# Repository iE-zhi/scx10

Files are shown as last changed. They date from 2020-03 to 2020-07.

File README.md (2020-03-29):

# scx10
 scx10 uart controller实现用串口控制SCX10攀爬车的基础动作，包括前进后退、左右转向和车灯控制。
 控制板接口：
 - 一路有刷电机
 - 两路舵机接口
 - 一个串口控制端
 - 一组前后灯和一组左右转向灯
 - 支持2S锂电池

控制板同样适用于符合以上条件的其他车辆及场景。

# 目录
- PCB: 电路板文件(AD18工程)
- program: 程序(keil5工程)
- 资料: 芯片资料

# PCB板尺寸
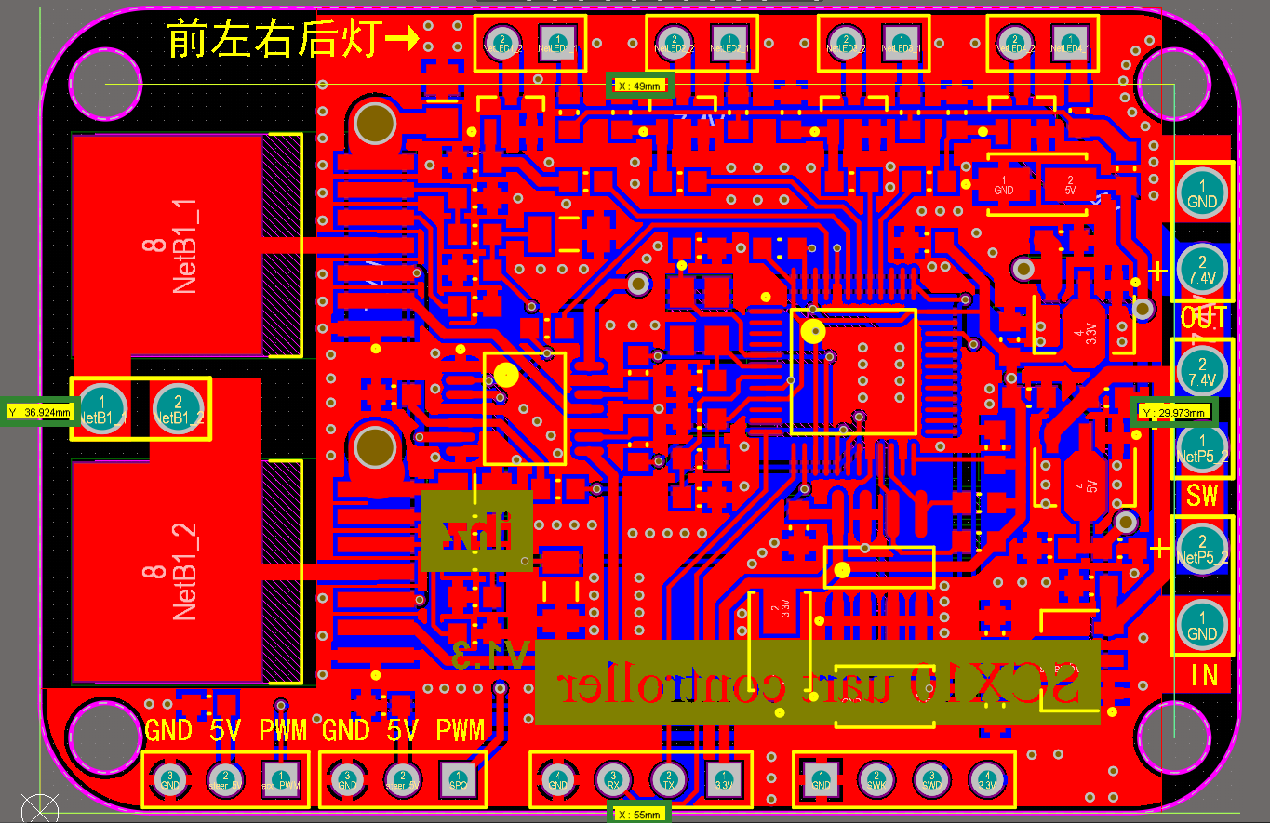
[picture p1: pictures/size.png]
pcb


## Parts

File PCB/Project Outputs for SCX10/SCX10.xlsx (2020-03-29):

Comment | Description | Designator | Footprint | LibRef | Quantity
Motor | Motor, General Kind | B1 | 7.4V | Motor | 1
0.1uF | Capacitor | C1, C2, C7, C9, C16, C19, C21, C22, C23, C24, C27 | C0603 | Cap | 11
4.7uF/16V | Capacitor | C3, C4 | 6-0805_M | Cap | 2
10uF | Capacitor | C5, C6, C8, C15, C18 | C0603 | Cap | 5
22uF | Capacitor | C10, C17, C20 | C0603 | Cap | 3
30pF | Capacitor | C25, C26 | C0603 | Cap | 2
3.6V | Schottky Diode | D1, D2 | C1206 | D Schottky | 2
SMAJ5.0CA |  | D3, D4, D5 | DO-214AC | SMAJ5.0CA | 3
F_LED | Header, 2-Pin | LED1 | HDR1X2 | Header 2 | 1
L_LED | Header, 2-Pin | LED2 | HDR1X2 | Header 2 | 1
R_LED | Header, 2-Pin | LED3 | HDR1X2 | Header 2 | 1
B_LED | Header, 2-Pin | LED4 | HDR1X2 | Header 2 | 1
Header 3 | Header, 3-Pin | P1, P2 | HDR1X3 | Header 3 | 2
Header 4 | Header, 4-Pin | P3 | HDR1X4 | Header 4 | 1
7.4V | Header, 2-Pin | P5, P6 | 7.4V | Header 2 | 2
SW | Header, 4-Pin | P7 | HDR1X4 | Header 4 | 1
NPN |  | Q3, Q4, Q5, Q6 | SOT23-3 | NPN | 4
0R/NC | Resistor | R2 | R0603 | Res2 | 1
240R | Resistor | R3, R4, R5, R6 | R0603 | Res2 | 4
10K | Resistor | R7, R8, R9, R10, R11, R12, R35 | R0603 | Res2 | 7
4.7K | Resistor | R13, R14, R15, R26, R27 | R0603 | Res2 | 5
1K | Resistor | R16, R17, R18, R19, R20, R21 | R0603 | Res2 | 6
510R | Resistor | R22, R23, R24, R25 | R0603 | Res2 | 4
SW-PB | Switch | S1 | 7.4V | SW-PB | 1
SN74LV125A-PW |  | U1 | TSSOP-14 | SN74LV125A-PW | 1
24C02 |  | U2 | SOP-8 | 24C02 | 1
BTN7971B |  | U3, U8 | INF-PG-TO263-7-1_L - Cloned | INF-BTN79XXX-PG-TO263-7-1-8 | 2
AMS1117-5V |  | U4, U6 | SOT-89 | AMS1117 | 2
AMS1117-3.3V |  | U5 | SOT-89 | AMS1117 | 1
STM32F103C8T6 |  | U7 | STM-LQFP48-L | STM32F103C8T6 | 1
8M |  | X1 | XTAL-8M | XTAL-8M | 1

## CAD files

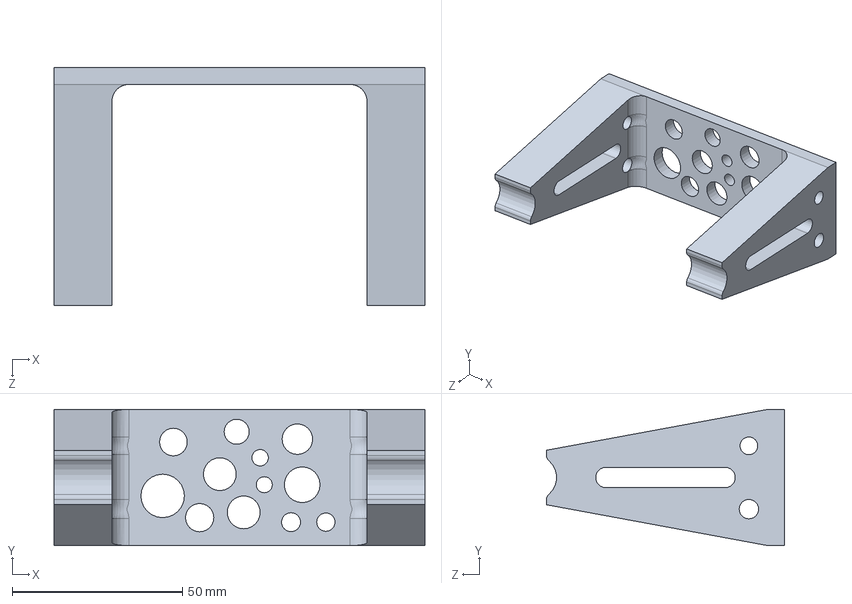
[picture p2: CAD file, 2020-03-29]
model/支撑.SLDPRT
109.0 x 40.0 x 70.0 mm

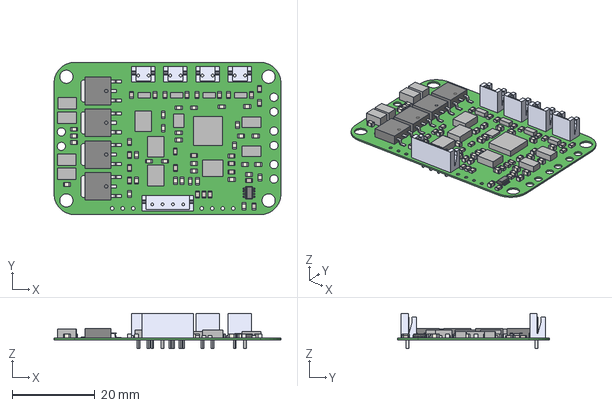
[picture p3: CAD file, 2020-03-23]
PCB/SCX10.step
55.0 x 36.9 x 8.50 mm

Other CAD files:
model/手柄.ipt
model/支撑.STL

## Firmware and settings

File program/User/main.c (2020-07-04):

#include "stm32f10x.h"
#include "delay.h"
#include "timer.h"
#include "controller.h"
#include "adc.h"

int main(void)
{
	u16 adc_L = 0;
	u16 adc_R = 0;
	float L_Voltage = 0.0;
	float R_Voltage = 0.0;
	float Current_Value = 0.0;
	
	delay_init();	    	 //延时函数初始化	  
	NVIC_PriorityGroupConfig(NVIC_PriorityGroup_2); 	 //设置NVIC中断分组2:2位抢占优先级，2位响应优先级
	
	LED_Init();
	uart2_init(115200);
	//24C02总线初始化
	AT24CXX_Init();			//IIC初始化
	Adc_Init();		  		//ADC初始化
  
	//有刷电机PWM初始化
	TIM3_PWM_Init(7199, 0);      //定时器3用于产生PWM控制有刷电机，PWM频率: 72M/7200 = 10KHz
	TIM_SetCompare1(TIM3,3599);
	TIM_SetCompare2(TIM3,3599);
	TIM_Cmd(TIM3, ENABLE);  //使能TIMx外设
	
	//使能有刷电机
	Enable_motor();
	
	//转向舵机PWM初始化
	TIM4_PWM_Init(19999, 71);      //定时器4产生50Hz的PWM控制舵机，比较值范围[999,1999]
	Servo_Value = AT24CXX_ReadLenByte(0x10, sizeof(Servo_Value));      //读取保存在24C02中的值
	Servo_Value = (Servo_Value >= 1099 && Servo_Value <= 1899) ? Servo_Value : 1499;
	TIM_SetCompare3(TIM4, Servo_Value);      //TIM4_CH3占空比7.5%,使舵机处于中间位置
	TIM_Cmd(TIM4, ENABLE);  //使能TIMx外设
	
	//转向灯定时器初始化
	TIM2_Int_Init(4999,7199);      //定时器2产生2Hz的频率控制转向灯闪烁
	//关闭转向灯
	veer_LED.L_LED_EN = 0;      //失能转向灯控制
	veer_LED.R_LED_EN = 0;
	L_LED = 0;      //关闭灯
	R_LED = 0;
	TIM_Cmd(TIM2, ENABLE);  //使能TIM2外设
	
	//读取过流保护值
	OC_Value = AT24CXX_ReadLenByte(0x1a, sizeof(OC_Value));
	OC_Value = (OC_Value >= 2 && OC_Value <=30) ? OC_Value : 4; 
	
	while (1)
  {
		adc_L = Get_Adc_Average(ADC_Channel_5,10);
		L_Voltage = (float)adc_L*(3.3/4096);
		adc_R = Get_Adc_Average(ADC_Channel_5,10);
		R_Voltage = (float)adc_R*(3.3/4096);
		Current_Value = (L_Voltage + R_Voltage) / 2 * 19.5;
		if (Current_Value > OC_Value)
		{
			// 关闭电机
			TIM_SetCompare1(TIM3,0);
			TIM_SetCompare2(TIM3,0);
			// 关闭串口
			USART_Cmd(USART2, DISABLE);
		}
		delay_ms(20);
  }
}


/******************* 微意电子 *****END OF FILE****/

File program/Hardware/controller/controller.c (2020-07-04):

/*
/ 2020.3.14 指定基础命令，实现串口数据解析，控制车的动作
* CRC校验码由前面所有字节校验得到
*
- 有刷电机和舵机控制指令 -
| 包头   命令   电机方向   电机速度   舵机方向   舵机角度   CRC16低字节   CRC16高字节  结束符
| 0x23   0xa5   0x56(正)   0x00~0xff  0x58(左)   0x00~0xff     0x00          0x00       \r\n
|               0x65(反)              0x85(右)
|               0x88(停)              0x88(中心)
*
- 灯控制命令 -
| 包头   命令   前灯   后灯   左转向灯   右转向灯   CRC16低字节   CRC16高字节   结束符
| 0x23   0xa6   0x01   0x01     0x01       0x01        0x00          0x00        \r\n   (所有灯0x01为开,0x00为关)
*
- 舵机中心微调命令 - 
| 包头   命令   舵机方向   CRC16低字节   CRC16高字节   结束符
| 0x23   0xa8   0x85(左)      0x00          0x00        \r\n
|               0x58(右)
|               0x88(恢复默认的值 Servo_Value=1499)
*
- 舵机中心值保存命令 -
| 包头   命令   CRC16低字节   CRC16高字节   结束符
| 0x23   0xb0      0x00          0x00        \r\n
*
/ 2020.3.15 添加过流保护指令 
- 设置过流保护值命令 -
| 包头   命令     过流保护值   CRC16低字节   CRC16高字节   结束符
| 0x23   0xb2   0x00~1E(0-30A)    0x00          0x00        \r\n
*
* 串口数据接收存放变量USART_RX_BUF
*/
#include "controller.h"

struct LED veer_LED;

int Servo_Value = 1499;    // 转向舵机中心值
//int Acc_Value = 1499;   // 油门舵机中心值
u8 OC_Value = 4;      // 默认过流保护值

// 电机控制
static void Motor_control(void)
{
	float Speed_Value = 0.0;
	
	Speed_Value = (float)USART_RX_BUF[3] / 255.0 * 3599 + 0.5;
	if ((unsigned int)Speed_Value == 0)
		USART_RX_BUF[2] = 0x88;
	switch(USART_RX_BUF[2])
	{
		case 0x56: // 电机正转
			(3600+(int)Speed_Value<=7199) ? TIM_SetCompare1(TIM3,3600 + (int)Speed_Value) : TIM_SetCompare1(TIM3, 7199);
			(3599-(int)Speed_Value>=0) ? TIM_SetCompare2(TIM3,3599 - (int)Speed_Value) : TIM_SetCompare1(TIM3, 0);
			break;
		case 0x65: // 电机反转
			(3599-(int)Speed_Value>=0) ? TIM_SetCompare1(TIM3,3599 - (int)Speed_Value) : TIM_SetCompare1(TIM3, 0);
			(3600+(int)Speed_Value<=7199) ? TIM_SetCompare2(TIM3,3600 + (int)Speed_Value) : TIM_SetCompare1(TIM3, 7199);
			break;
		case 0x88: // 电机停转
			TIM_SetCompare1(TIM3,0);
			TIM_SetCompare2(TIM3,0);
			break;
		default:
			break;
	}
}	

// 使能电机控制
void Enable_motor(void)
{
	GPIO_InitTypeDef  GPIO_InitStructure;
 	
	RCC_APB2PeriphClockCmd(RCC_APB2Periph_GPIOB, ENABLE);

	GPIO_InitStructure.GPIO_Pin = GPIO_Pin_0;
	GPIO_InitStructure.GPIO_Mode = GPIO_Mode_Out_PP;
	GPIO_InitStructure.GPIO_Speed = GPIO_Speed_50MHz;
	GPIO_Init(GPIOB, &GPIO_InitStructure);
	
	GPIO_SetBits(GPIOB, GPIO_Pin_0);
}

// 舵机控制
static void Servo_control(void)
{
	float Angle_Value = 0.0;
	
	Angle_Value = (float)USART_RX_BUF[5] / 255.0 * 400 + 0.5;
	if ((unsigned int)Angle_Value == 0)
		USART_RX_BUF[4] = 0x88;
	switch(USART_RX_BUF[4])
	{
		case 0x85: // 左转
			(Servo_Value-(int)Angle_Value >= 1099) ? TIM_SetCompare3(TIM4, Servo_Value - (int)Angle_Value) : TIM_SetCompare3(TIM4, 1099);
			break;
		case 0x58: // 右转
			(Servo_Value+(int)Angle_Value <= 1899) ? TIM_SetCompare3(TIM4, Servo_Value + (int)Angle_Value) : TIM_SetCompare3(TIM4, 1899);
			break;
		case 0x88: // 中心
			TIM_SetCompare3(TIM4, Servo_Value);
		default:
			break;
	}
}

//车灯IO口初始化
void LED_Init(void)
{
 GPIO_InitTypeDef  GPIO_InitStructure;
 	
 RCC_APB2PeriphClockCmd(RCC_APB2Periph_GPIOB, ENABLE);	 //使能PB端口时钟
	
 GPIO_InitStructure.GPIO_Pin = GPIO_Pin_4 | GPIO_Pin_5 |GPIO_Pin_6 |GPIO_Pin_7;
 GPIO_InitStructure.GPIO_Mode = GPIO_Mode_Out_PP; 		 //推挽输出
 GPIO_InitStructure.GPIO_Speed = GPIO_Speed_50MHz;		 //IO口速度为50MHz
 GPIO_Init(GPIOB, &GPIO_InitStructure);					 //根据设定参数初始化端口
}

// 车灯控制
static void LED_control(void)
{
	if (USART_RX_BUF[2])
		F_LED = 1;
	else
		F_LED = 0;
	if (USART_RX_BUF[3])
		B_LED = 1;
	else
		B_LED = 0;
	if (USART_RX_BUF[4])
		veer_LED.L_LED_EN = 1;
	else
	{
		veer_LED.L_LED_EN = 0;
		L_LED = 0;
	}
	if (USART_RX_BUF[5])
		veer_LED.R_LED_EN = 1;
	else
	{
		veer_LED.R_LED_EN = 0;
		R_LED = 0;
	}
}

//转向舵机微调
static void Servo_FineTuning(void)
{
	switch(USART_RX_BUF[2])
	{
		case 0x58: //向左微调
			if (Servo_Value > 1099)
			{
				Servo_Value--;
				TIM_SetCompare3(TIM4, Servo_Value);
			}
			break;
		case 0x85: //向右微调
			if (Servo_Value < 1899)
			{
				Servo_Value++;
				TIM_SetCompare3(TIM4, Servo_Value);
			}
			break;
		case 0x88: //恢复默认的值
			Servo_Value = 1499;
			TIM_SetCompare3(TIM4, Servo_Value);
			break;
		default:
			break;
	}
}

//保存舵机中心值
static void Save_ServoValue(void)
{
	AT24CXX_WriteLenByte(0x10, Servo_Value, sizeof(Servo_Value));
}

//保存过流保护值
static void Set_OCValue(void)
{
	OC_Value = USART_RX_BUF[2];
	AT24CXX_WriteLenByte(0x1a, OC_Value, sizeof(OC_Value));
}

void para_usart_data(void)
{
	unsigned short cal_crc = 0;
	unsigned short rec_crc = 0;

	rec_crc = (USART_RX_BUF[(USART_RX_STA&0X3FFF)-1] << 8) | USART_RX_BUF[(USART_RX_STA&0X3FFF)-2];
	cal_crc = CRC16((char*)USART_RX_BUF);
	if (USART_RX_BUF[0] == '#' && cal_crc == rec_crc)
	{
		switch(USART_RX_BUF[1])
		{
			case 0xa5: // 电机、舵机控制
				Motor_control();
				Servo_control();
				break;
			case 0xa6: // 车灯控制
				LED_control();
				break;
			case 0xa8: // 舵机微调
				Servo_FineTuning();
				break;
			case 0xb0: // 舵机中心值保存
				Save_ServoValue();
				break;
			case 0xb2: // 设置过流保护值
				Set_OCValue();
				break;
			default:
				break;
		}
	}
}

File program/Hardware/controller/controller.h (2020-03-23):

#ifndef __CONTROLLER_H__
#define __CONTROLLER_H__

#include "stm32f10x.h"
#include "usart.h"
#include "sys.h"
#include "24cxx.h"
#include "crc16.h"

#define F_LED PBout(4)
#define B_LED PBout(7)
#define L_LED PBout(5)
#define R_LED PBout(6)

struct LED
{
	unsigned char L_LED_EN : 1;
	unsigned char R_LED_EN : 1;
};

extern struct LED veer_LED;
extern int Servo_Value;
extern u8 OC_Value;
//extern int Acc_Value;

void para_usart_data(void);
void LED_Init(void);
void Enable_motor(void);

#endif

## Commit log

2020-03-23 SCX10 V1.2
    [SCX10.xlsx]
2020-03-29 PCB V1.3
    [SCX10.xlsx, driver.SchDoc, power.SchDoc]
2020-03-29 add Suspended frame
    [支撑.SLDPRT, 支撑.STL]
2020-04-02 repair program
    Fixed an issue where the program would crash after receiving incorrect data
    [usart.c]
2020-04-13 更新stm32封装
    [SCX10.SchDoc]
2020-07-04 adjust servo
